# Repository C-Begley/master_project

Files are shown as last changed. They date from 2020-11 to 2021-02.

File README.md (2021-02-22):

# MEng Individual Project ENG5041PA Hardware and Software Emulation Testbed for CubeSat Design

## Abstract
CubeSats are praised for reducing the cost of access to space and increasing opportunities for universities and small organisations to carry out space related research. In principal, a small team with an innovative solution could rapidly develop and fly hardware in space using already existing building 'block' components. However, they still require technical electronic knowledge for the construction and testing of designs. While technical knowledge will always be required, especially on custom built CubeSats, this project aimed to reduce this barrier of entry, by providing a test bed framework to program and experiment with potential CubeSat designs.

The project has two main aims: the construction of physical devices for use in testing and developing accompanying software to help use these devices. The main physical device is a FlatSat, which aims to be generic and suitable for a range of projects. It uses PC/104 Plus connectors and has access to power and diagnostic connections. Alongside the FlatSat, there is a mainboard and battery board from an open source CubeSat design, which can be used to test other CubeSat subsystems. 

The project software helps schedule tasks to be run using the mainboard and FlatSat system. These tasks then act as emulations of an entire CubeSat subsystem. This allows for a subsystem to be tested, as if an entire CubeSat had already been constructed. The framework for programming and using this software, strives to be simple enough for those inexperienced with programming to be able to be use, while still giving enough complexity that most aspects of a CubeSat can be emulated.

To demonstrate the usability of the system, two demonstration boards have been constructed. These boards provide example emulations of payload and communication boards. They also provide a template that can be modified to construct and emulate other subsystems.  A demonstration task schedule has also been created to show how devices can interact with the software and mainboard from this project.

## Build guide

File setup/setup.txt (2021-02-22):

SETUP PYCUBED BOARD:
1.Follow the instructions on : https://www.notion.so/Programming-the-Bootloader-a5c2f6b50c3d459eaa0a4f00d8218365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
(In case site is taken down, see Programming the BootLoader.pdf)

2.The device should connect to a computer as a external drive. Transfer via USB all the files in software/Mainboard
(If it hasn't connected, try debugging with Atmel or following PyCubed FAQ/advice. I never got to run the Pycubed board(used Grand Central Metro M4 instead), so can't offer more advice)

SETUP MAIN PROGRAM:
OPTION ONE: Automatic Running
1. Rename the file `run_main.py` to main
2. Restart the device
3. The main program should run all tasks in the demo file

OPTION TWO: Manually running the code 
(This is often the best option, as main.py files can sometimes cause issue in Ciruit Python)

1.Run the code from a REPL programm
 `import run_main as m`

a. Linux users can use Picocom 
b. Mac users can use screen or Mu
c. Windows users can use Mu  
(Other programs may also work, this is not an exhaustive list)

Notes:
If you wish to use a different folder for running your code, 
replace the name PROJECT_FOLDER in the file run_main.py with something else.
 The new folder should follow the same structure and subfolders as demo

See Thesis Pgs.40-49 for more information on the options within a task, interupt and device file

SETUP DEMONSTRATION BOARDS:
The code for the demonstration boards is in MicroPython, to support using the device as a slave.
Some Circuit Python libraries etc will not work on these boards and vice versa

The boards provided in the lab should already be flashed. If not follow the steps in Flashing.txt (they are written for a Linux device)

To transfer files to these boards, ampy has to be used 
e.g `ampy -- port /deb/ttyUSB0 coms_IWC.py`
(This should work on Mac or Linux but may need to be installed)

There are two programs that can be run on the boards
`payload_main.py` and `coms_main.py` 

To use the payload add the `payload_main.py`, `demo_adc.py` and `payload_I2C.py`

To use the communication board add `coms_main.py` and `coms_I2C.py`

To run on a terminal, use a REPL program (see above)
`import payload_main as pld`
           or
`import coms_main as cms`

You can also just run the commands inside a REPL terminal

Like with the other files, you can rename them to main. However, this omes with the caveat the boards may need reflashing

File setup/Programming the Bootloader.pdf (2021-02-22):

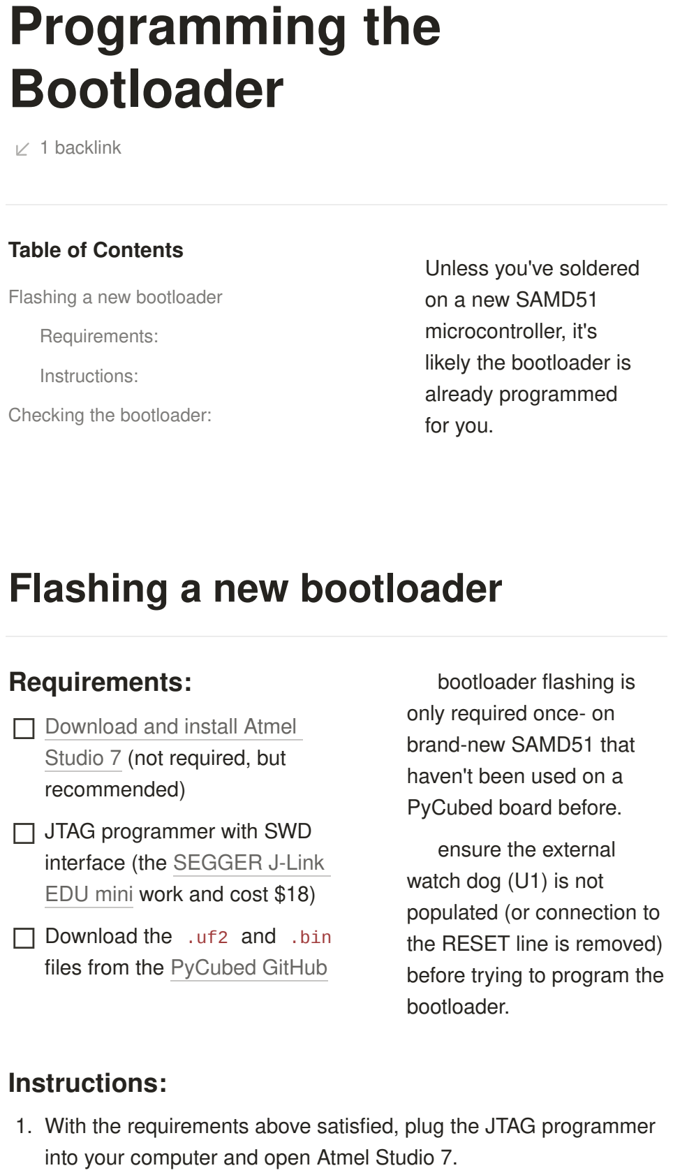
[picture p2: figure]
1 backlink; Programming the Bootloader; Table of Contents; Flashing a new bootloader; Requirements:; Instructions:; Checking the bootloader:; Unless you've soldered on a new SAMD51; microcontroller, it's; likely the bootloader is; already programmed for you.; (not required, but; recommended); JTAG programmer with SWD; interface (the work and cost $18); Download the .uf2 and .bin files from the; bootloader flashing is; only required once- on brand-new SAMD51 that; haven't been used on a PyCubed board before.; ensure the external; watch dog (U1) is not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

1. With the requirements above satisfied, plug the JTAG programmer into your computer and open Atmel Studio 7.
Programming the Bootloader | https://www.notion.so/Programming-the-Bootloader-a5...
1 of 6 | 22/02/2021, 15:24

2. Navigate to Tools → Device Programming, as shown:
3. Select the appropriate Tool and Device from the drop-down menus and click apply.

make sure to choose the correct microcontroller part number. Visually check the part markings on the SAMD51 to confirm if it's the SAMD51x19 or SAMD51x20.

4. Navigate to "Memories" on the left-hand side.
5. Uncheck the "Erase Flash before programming" box, and then click the "..." button, as shown:
6. Navigate to the directory you saved the GitHub firmware files, and change the file parameters from "Programming Files" to "Binary" and shown:

7. Select the .bin file downloaded previously and click the "Open" button:

8. Now make the following connections to the PyCubed board. If you're careful, you can avoid soldering header-pins to the board by just holding jumper-wire pins (or pogo pins, if you have them) against the through-holes during programming. When in doubt, solder the header pins.

Required Connections:

Main micro USB cable (to provide power)

Note: it's good practice to use a multimeter and confirm 3.3V is present when the USB connection is made to the PyCubed board. If the voltage doesn't read 3.3V between "3V3" and "GND" you need to troubleshoot that first.

VTref (connected to 3V3)

TMS (connected to SWDIO)

TCK (connected to SWCLK)

GND (connected to GND)

9. With the connections made, return to Atmel Studio 7 and click the "Read" button. A device signature should populate. If an error appears, check connections and troubleshoot the specific error message.

Common Errors

10. After receiving a device signature, click the "Program" button. Programming should only take a few moments.
11. Successful bootloader programming will trigger the PyCubed board to reboot. After a few moments, the board should mount to the computer as a PYCUBEDBOOT drive.

### Flashing the Firmware:

12. Drag the CircuitPython firmware .uf2 file downloaded previously to the PYCUBEDBOOT drive:
13. As soon as the file is done transferring, the board will reboot again and mount as CIRCUITPY or PYCUBED and is now a functioning CircuitPython board. Congratulations!
Note: now is a good time to load the | to the lib
folder as described in: Adding/Updating Libraries
14. The firmware loaded in step 12 makes it possible to safely solder the external watch dog (U1) onto the board.

# Checking the bootloader:

1. Connect the PyCubed board to your computer via USB
2. Quickly double-click the "RESET" button located on the top of the board

The pace of the double-click can be difficult. If it doesn't work,

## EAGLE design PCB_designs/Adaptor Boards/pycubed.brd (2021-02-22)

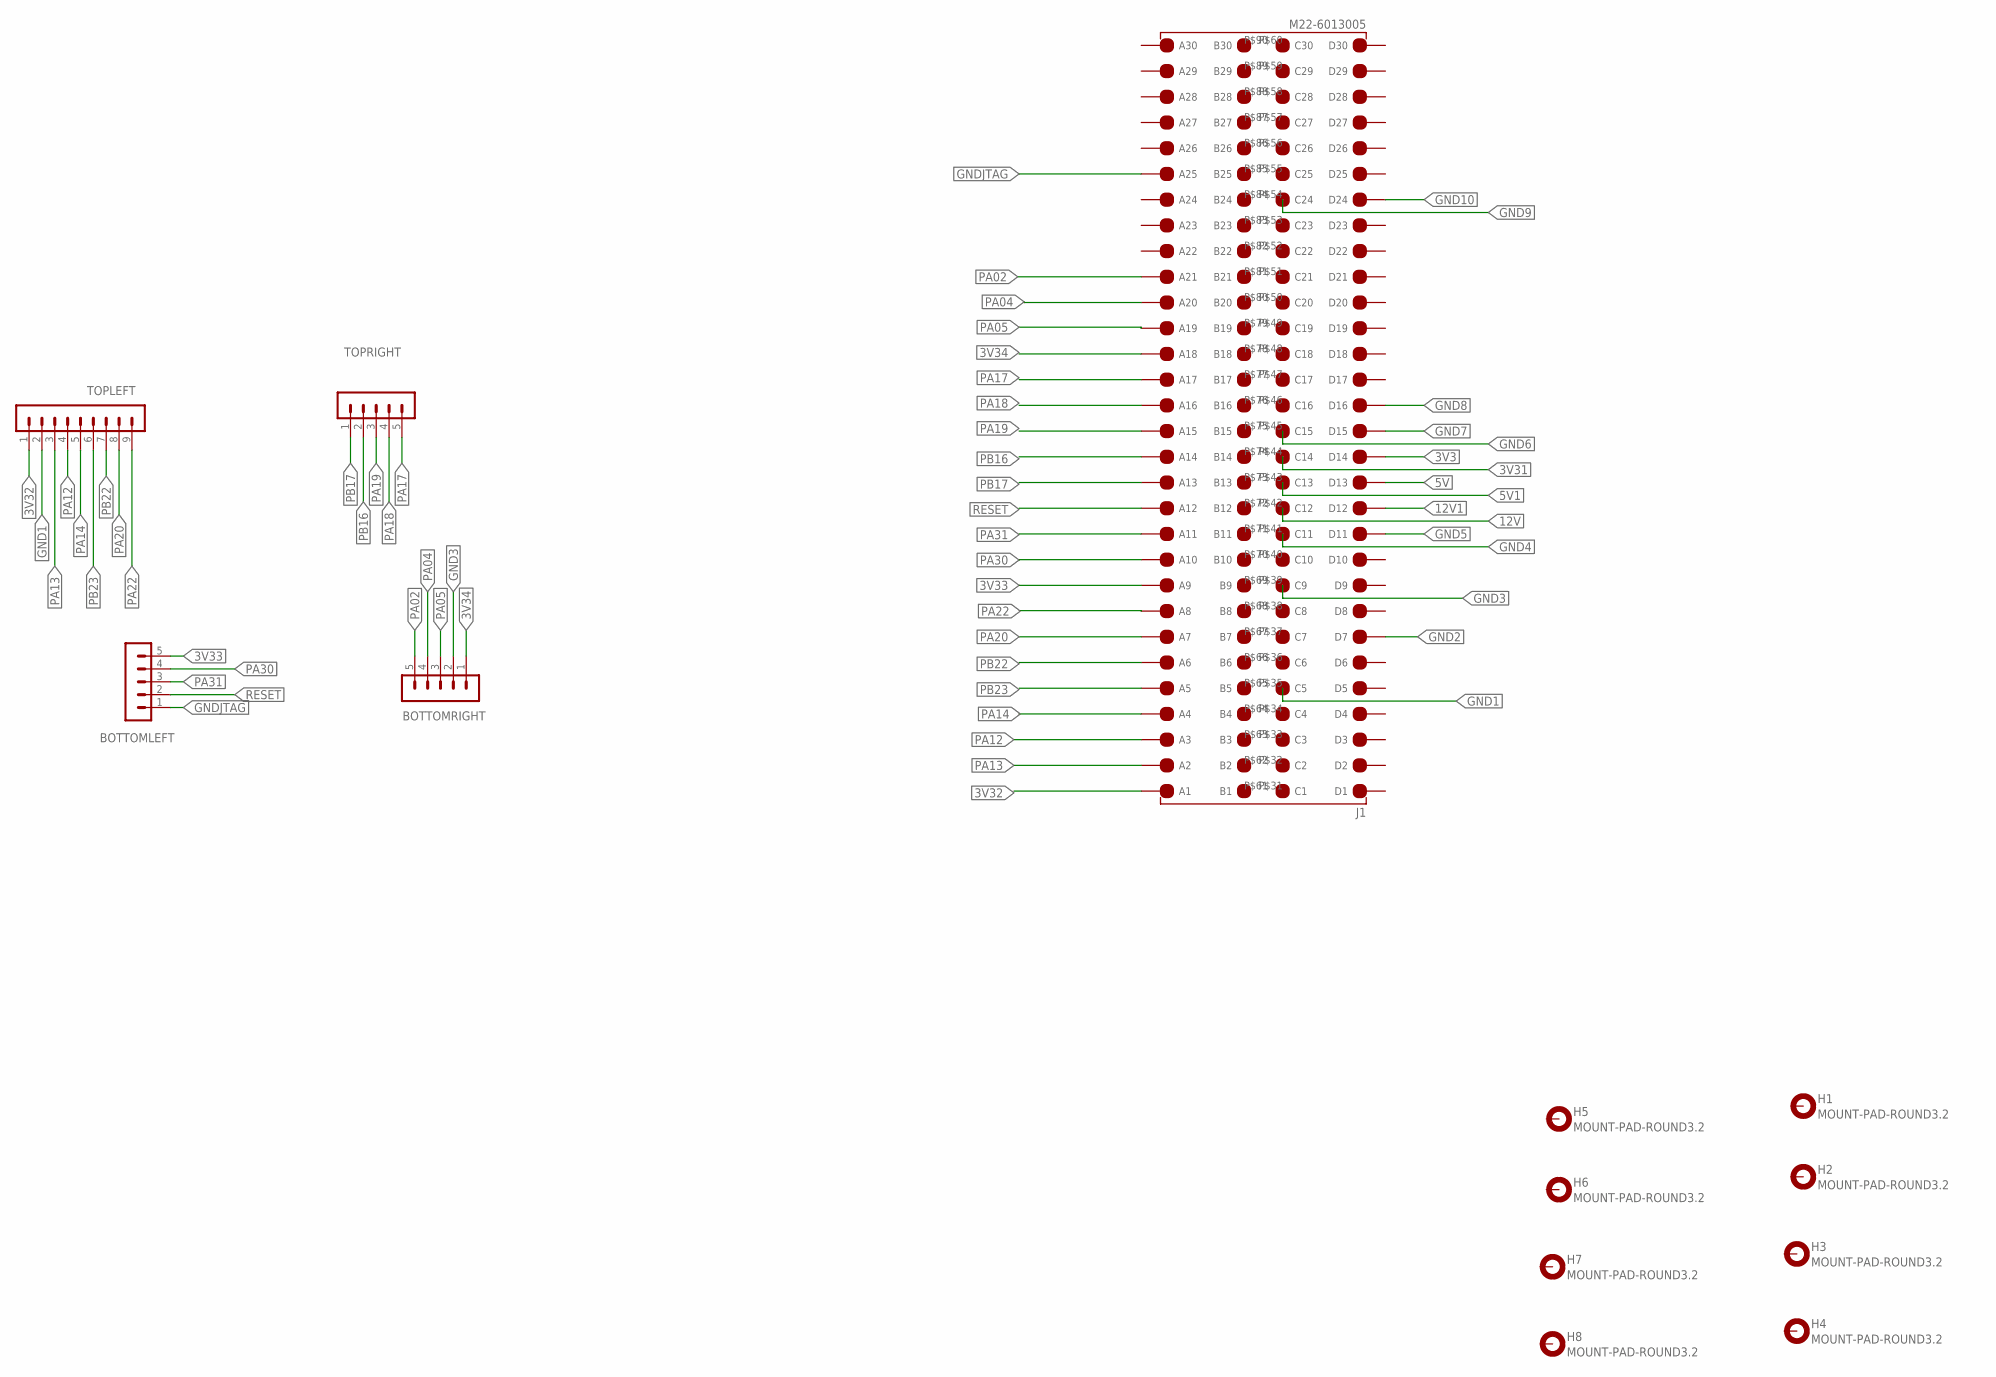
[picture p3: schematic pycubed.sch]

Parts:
BOTTOMLEFT: MA05-1
BOTTOMRIGHT: MA05-1
H1, H2, H3, H4, H5, H6, H7, H8: MOUNT-PAD-ROUND3.2; 3,2-PAD
J1: M22-6013005; RHDR120W55P200_4X30_6020X820X9
TOPLEFT: MA09-1
TOPRIGHT: MA05-1

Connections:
3V3: J1.P$14 (D14)
3V31: J1.P$44 (C14)
3V32: J1.P$91 (A1), TOPLEFT.1
3V33: BOTTOMLEFT.5, J1.P$99 (A9)
3V34: BOTTOMRIGHT.1, J1.P$108 (A18)
5V: J1.P$13 (D13)
5V1: J1.P$43 (C13)
12V: J1.P$42 (C12)
12V1: J1.P$12 (D12)
GND1: J1.P$35 (C5), TOPLEFT.2
GND2: J1.P$7 (D7)
GND3: BOTTOMRIGHT.2, J1.P$39 (C9)
GND4: J1.P$41 (C11)
GND5: J1.P$11 (D11)
GND6: J1.P$45 (C15)
GND7: J1.P$15 (D15)
GND8: J1.P$16 (D16)
GND9: J1.P$54 (C24)
GND10: J1.P$24 (D24)
GNDJTAG: BOTTOMLEFT.1, J1.P$115 (A25)
PA02: BOTTOMRIGHT.5, J1.P$111 (A21)
PA04: BOTTOMRIGHT.4, J1.P$110 (A20)
PA05: BOTTOMRIGHT.3, J1.P$109 (A19)
PA12: J1.P$93 (A3), TOPLEFT.4
PA13: J1.P$92 (A2), TOPLEFT.3
PA14: J1.P$94 (A4), TOPLEFT.5
PA17: J1.P$107 (A17), TOPRIGHT.5
PA18: J1.P$106 (A16), TOPRIGHT.4
PA19: J1.P$105 (A15), TOPRIGHT.3
PA20: J1.P$97 (A7), TOPLEFT.8
PA22: J1.P$98 (A8), TOPLEFT.9
PA30: BOTTOMLEFT.4, J1.P$100 (A10)
PA31: BOTTOMLEFT.3, J1.P$101 (A11)
PB16: J1.P$104 (A14), TOPRIGHT.2
PB17: J1.P$103 (A13), TOPRIGHT.1
PB22: J1.P$96 (A6), TOPLEFT.7
PB23: J1.P$95 (A5), TOPLEFT.6
RESET: BOTTOMLEFT.2, J1.P$102 (A12)

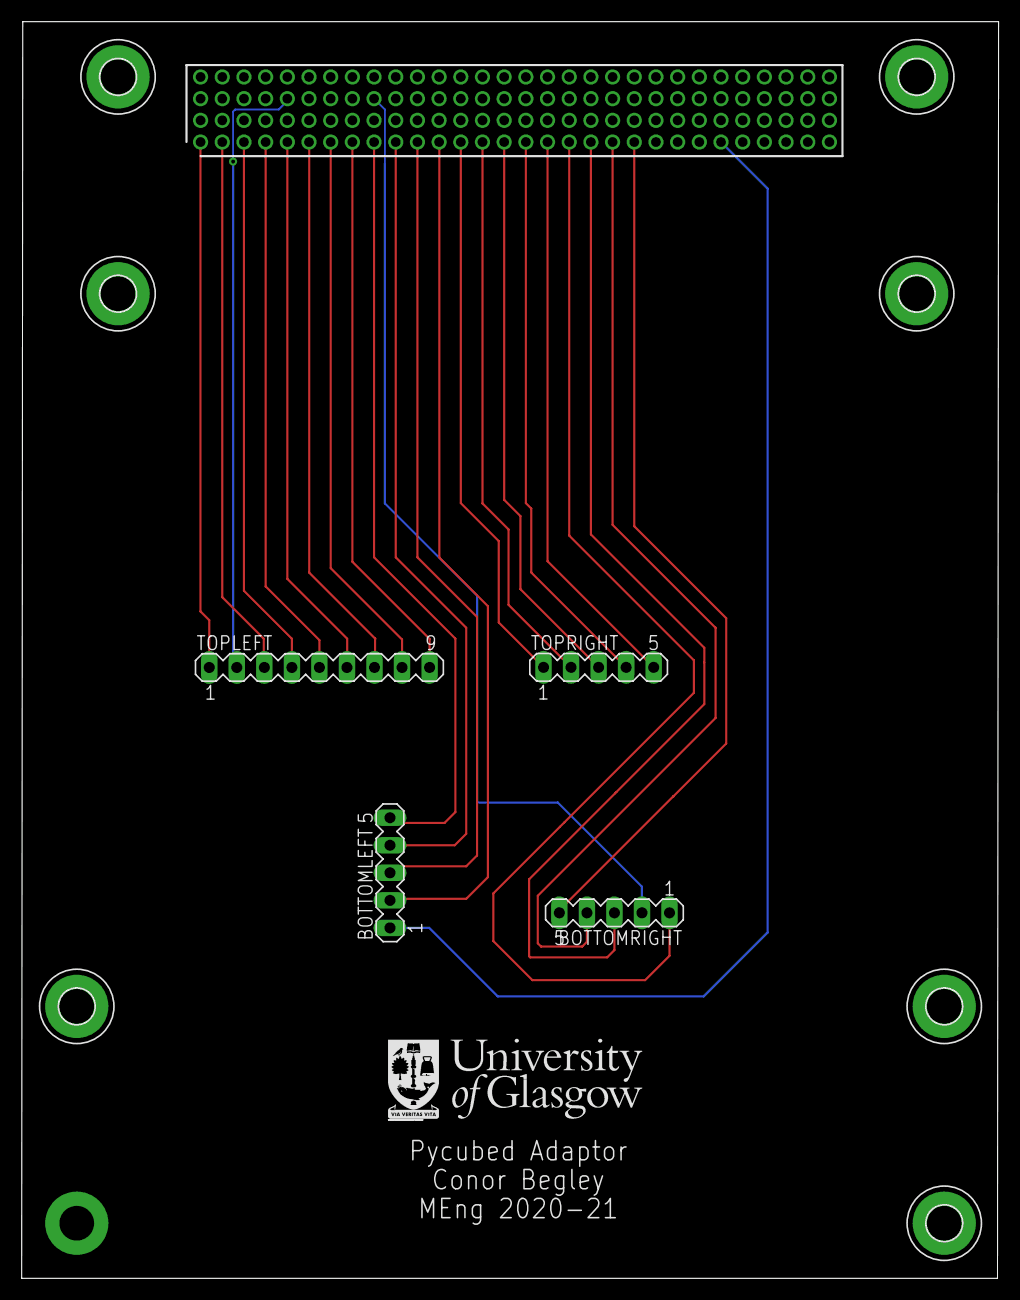
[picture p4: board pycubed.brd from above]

Board: 2 copper layers, 90.1 x 115.9 mm, 13 parts (1 on the bottom side), 24 nets.

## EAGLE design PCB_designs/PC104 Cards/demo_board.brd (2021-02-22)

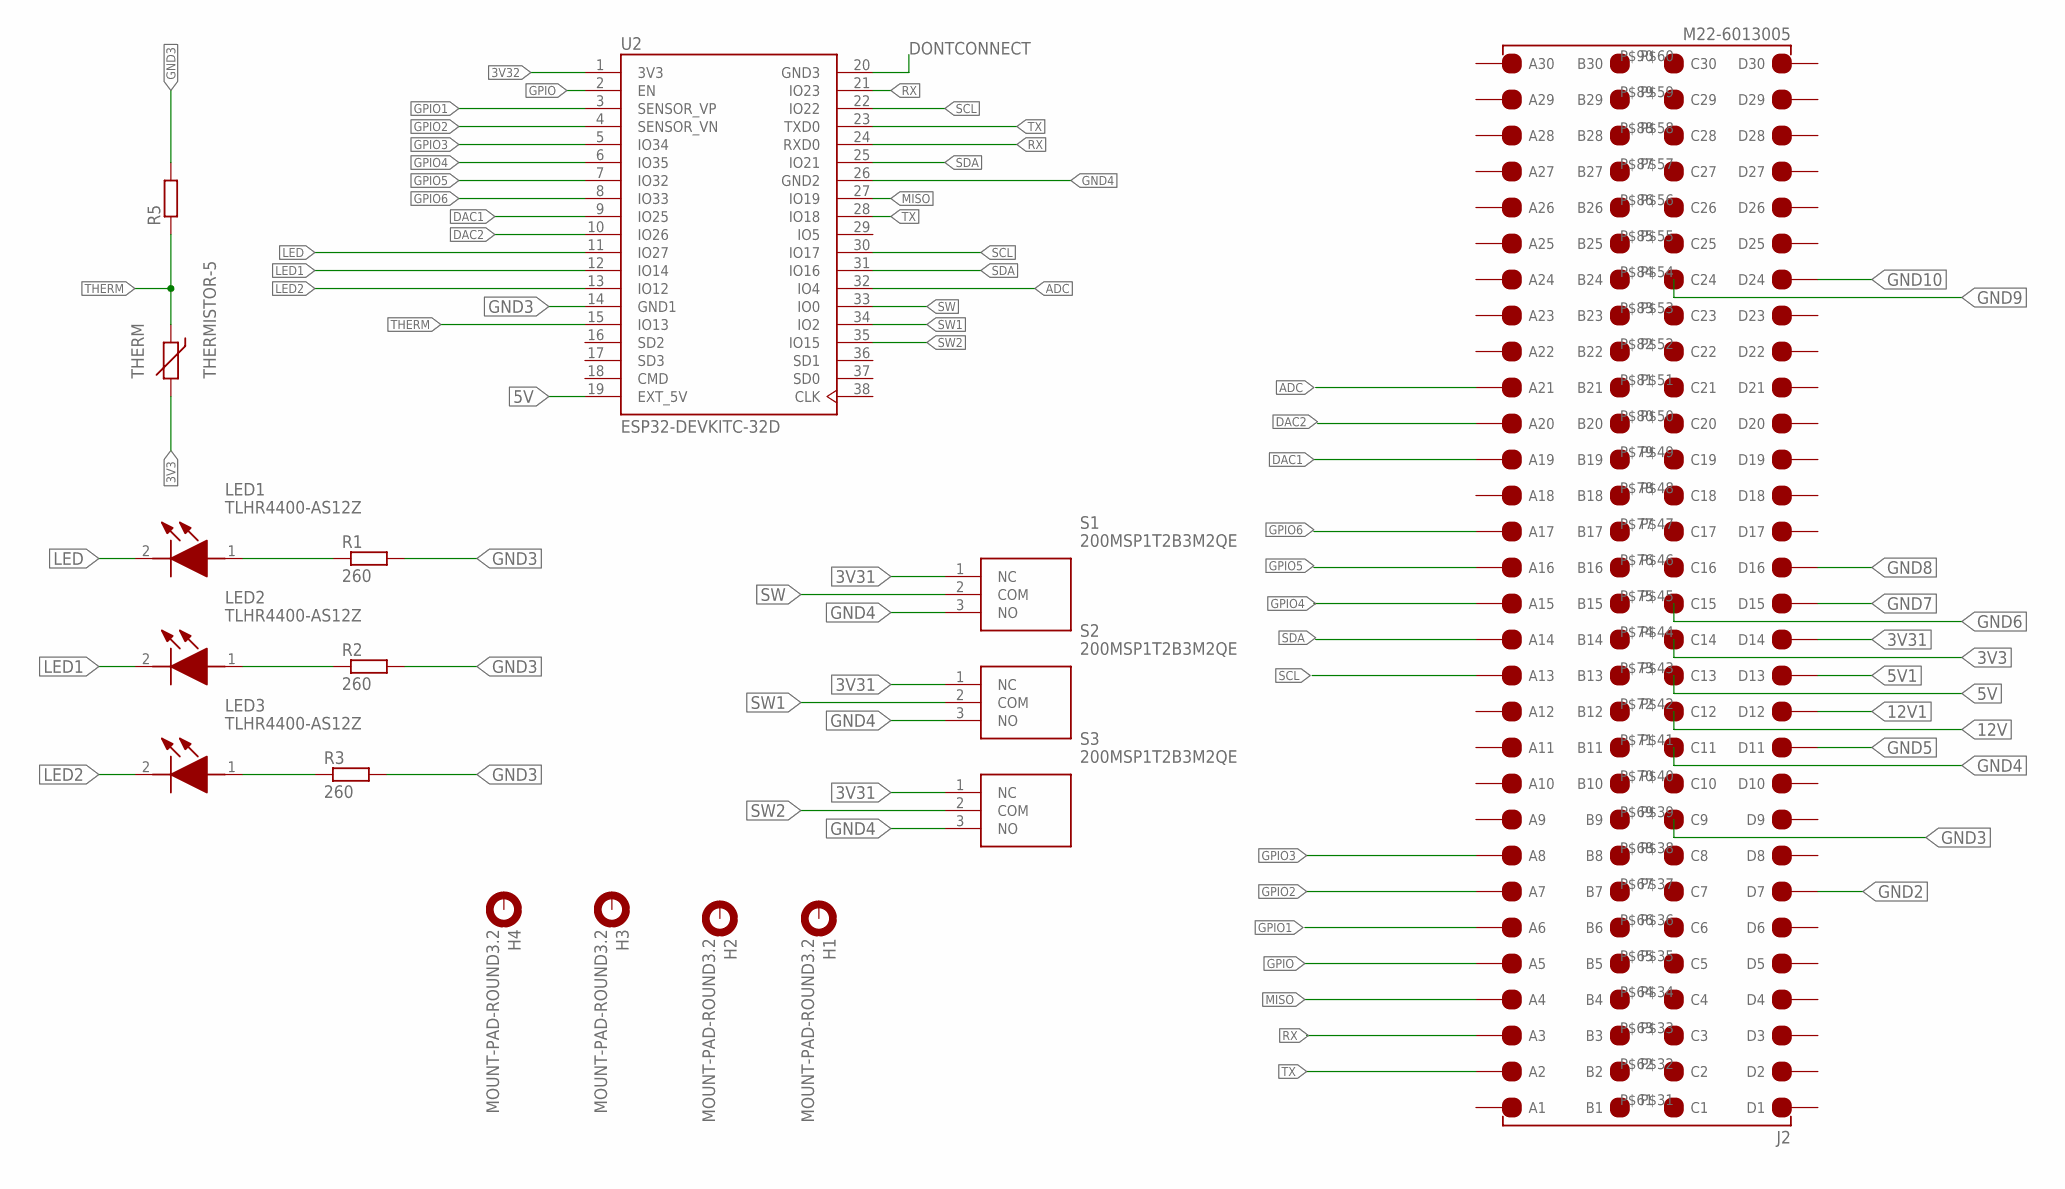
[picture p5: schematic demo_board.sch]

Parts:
H1, H2, H3, H4: MOUNT-PAD-ROUND3.2; 3,2-PAD
J2: M22-6013005; RHDR120W55P200_4X30_6020X820X9
LED1, LED2, LED3: TLHR4400-AS12Z; TLHR4400AS12Z
R1, R2, R3: 260; 0204/7
R5: 130; 0204/7
S1, S2, S3: 200MSP1T2B3M2QE
THERM: THERMISTOR-5; R-5
U2: ESP32-DEVKITC-32D; MODULE_ESP32-DEVKITC-32D

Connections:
3V3: J2.P$44 (C14), THERM.2
3V31: J2.P$14 (D14), S1.1 (NC), S2.1 (NC), S3.1 (NC)
3V32: U2.1 (3V3)
5V: J2.P$43 (C13), U2.19 (EXT_5V)
5V1: J2.P$13 (D13)
12V: J2.P$42 (C12)
12V1: J2.P$12 (D12)
ADC: J2.P$111 (A21), U2.32 (IO4)
DAC1: J2.P$109 (A19), U2.9 (IO25)
DAC2: J2.P$110 (A20), U2.10 (IO26)
DONTCONNECT: U2.20 (GND3)
GND2: J2.P$7 (D7)
GND3: J2.P$39 (C9), R1.2, R2.2, R3.2, R5.2, U2.14 (GND1)
GND4: J2.P$41 (C11), S1.3 (NO), S2.3 (NO), S3.3 (NO), U2.26 (GND2)
GND5: J2.P$11 (D11)
GND6: J2.P$45 (C15)
GND7: J2.P$15 (D15)
GND8: J2.P$16 (D16)
GND9: J2.P$54 (C24)
GND10: J2.P$24 (D24)
GPIO: J2.P$95 (A5), U2.2 (EN)
GPIO1: J2.P$96 (A6), U2.3 (SENSOR_VP)
GPIO2: J2.P$97 (A7), U2.4 (SENSOR_VN)
GPIO3: J2.P$98 (A8), U2.5 (IO34)
GPIO4: J2.P$105 (A15), U2.6 (IO35)
GPIO5: J2.P$106 (A16), U2.7 (IO32)
GPIO6: J2.P$107 (A17), U2.8 (IO33)
LED: LED1.2 (K), U2.11 (IO27)
LED1: LED2.2 (K), U2.12 (IO14)
LED2: LED3.2 (K), U2.13 (IO12)
MISO: J2.P$94 (A4), U2.27 (IO19)
unnamed: LED1.1 (A), R1.1
unnamed: LED2.1 (A), R2.1
unnamed: LED3.1 (A), R3.1
RX: J2.P$93 (A3), U2.21 (IO23), U2.24 (RXD0)
SCL: J2.P$103 (A13), U2.22 (IO22), U2.30 (IO17)
SDA: J2.P$104 (A14), U2.25 (IO21), U2.31 (IO16)
SW: S1.2 (COM), U2.33 (IO0)
SW1: S2.2 (COM), U2.34 (IO2)
SW2: S3.2 (COM), U2.35 (IO15)
THERM: R5.1, THERM.1, U2.15 (IO13)
TX: J2.P$92 (A2), U2.23 (TXD0), U2.28 (IO18)

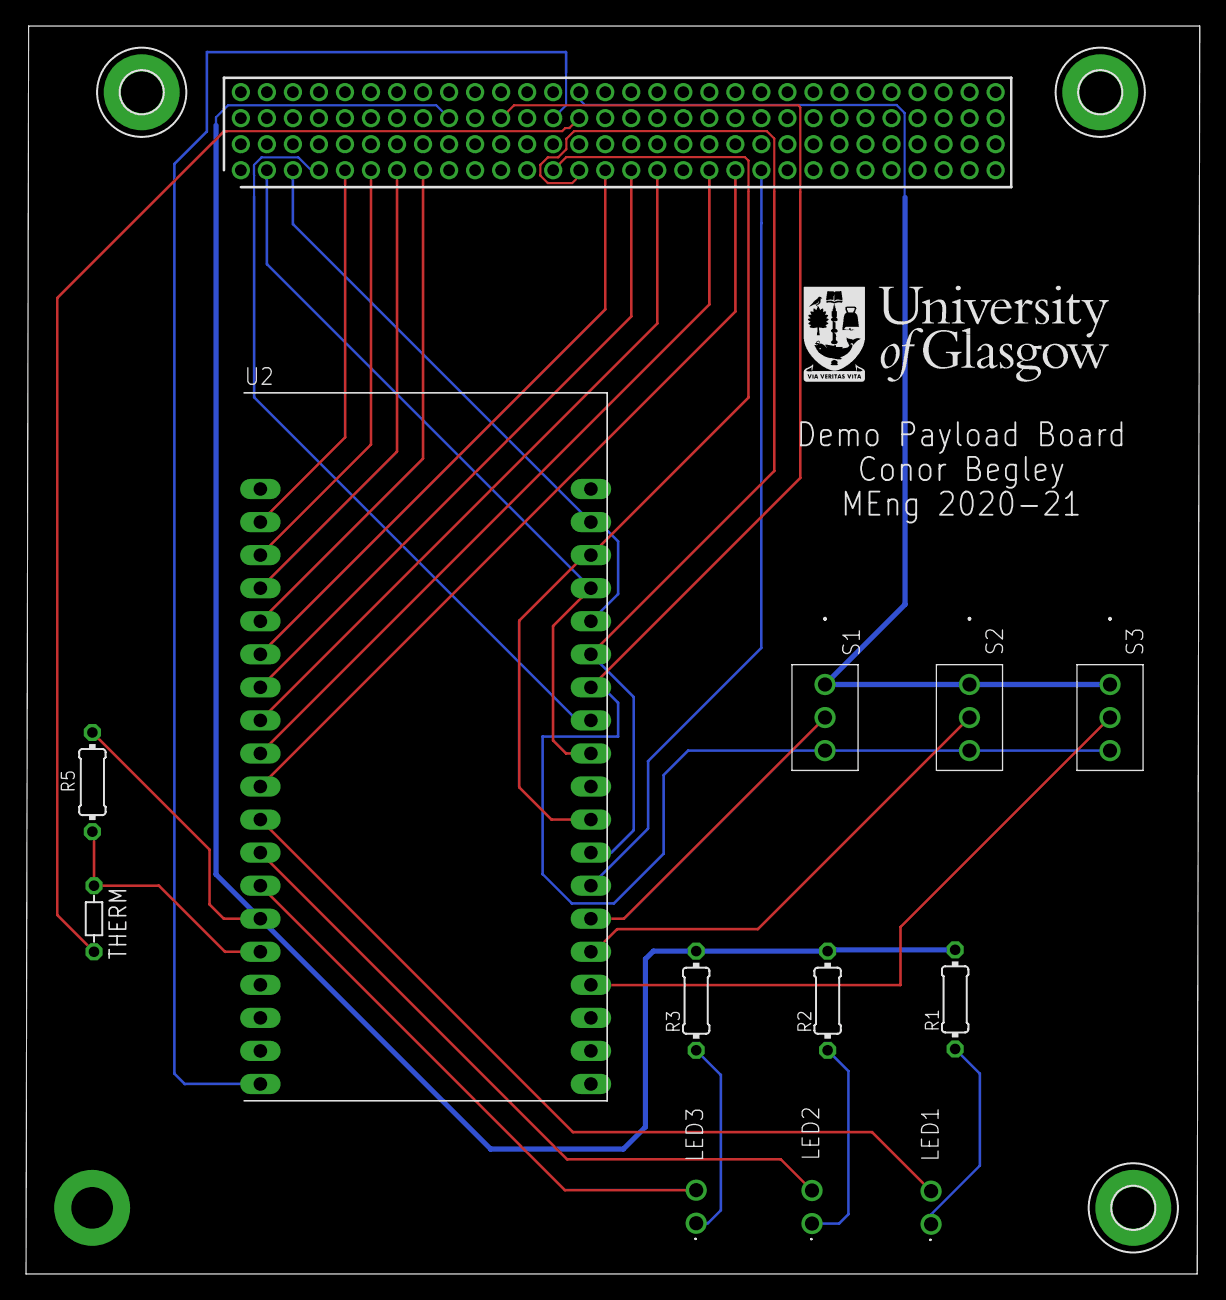
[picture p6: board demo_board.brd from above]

Board: 2 copper layers, 90.2 x 95.9 mm, 17 parts (1 on the bottom side), 30 nets.

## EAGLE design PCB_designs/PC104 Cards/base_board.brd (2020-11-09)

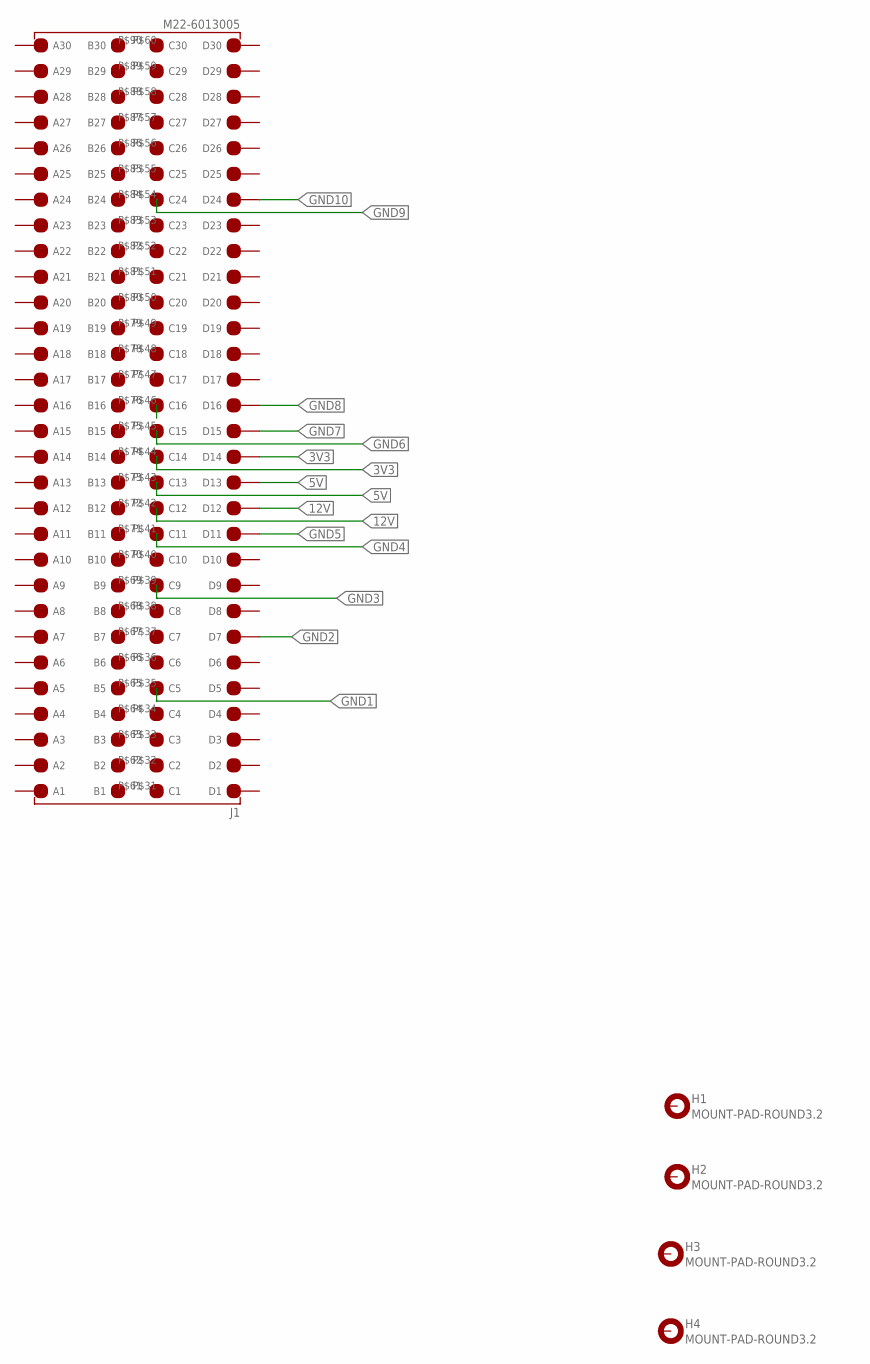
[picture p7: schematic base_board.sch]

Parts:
H1, H2, H3, H4: MOUNT-PAD-ROUND3.2; 3,2-PAD
J1: M22-6013005; RHDR120W55P200_4X30_6020X820X9

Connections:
3V3: J1.P$14 (D14), J1.P$44 (C14)
5V: J1.P$13 (D13), J1.P$43 (C13)
12V: J1.P$12 (D12), J1.P$42 (C12)
GND1: J1.P$35 (C5)
GND2: J1.P$7 (D7)
GND3: J1.P$39 (C9)
GND4: J1.P$41 (C11)
GND5: J1.P$11 (D11)
GND6: J1.P$45 (C15)
GND7: J1.P$15 (D15)
GND8: J1.P$16 (D16), J1.P$46 (C16)
GND9: J1.P$54 (C24)
GND10: J1.P$24 (D24)

Board: 2 copper layers, 5 parts (1 on the bottom side), 4 nets, no tracks yet.

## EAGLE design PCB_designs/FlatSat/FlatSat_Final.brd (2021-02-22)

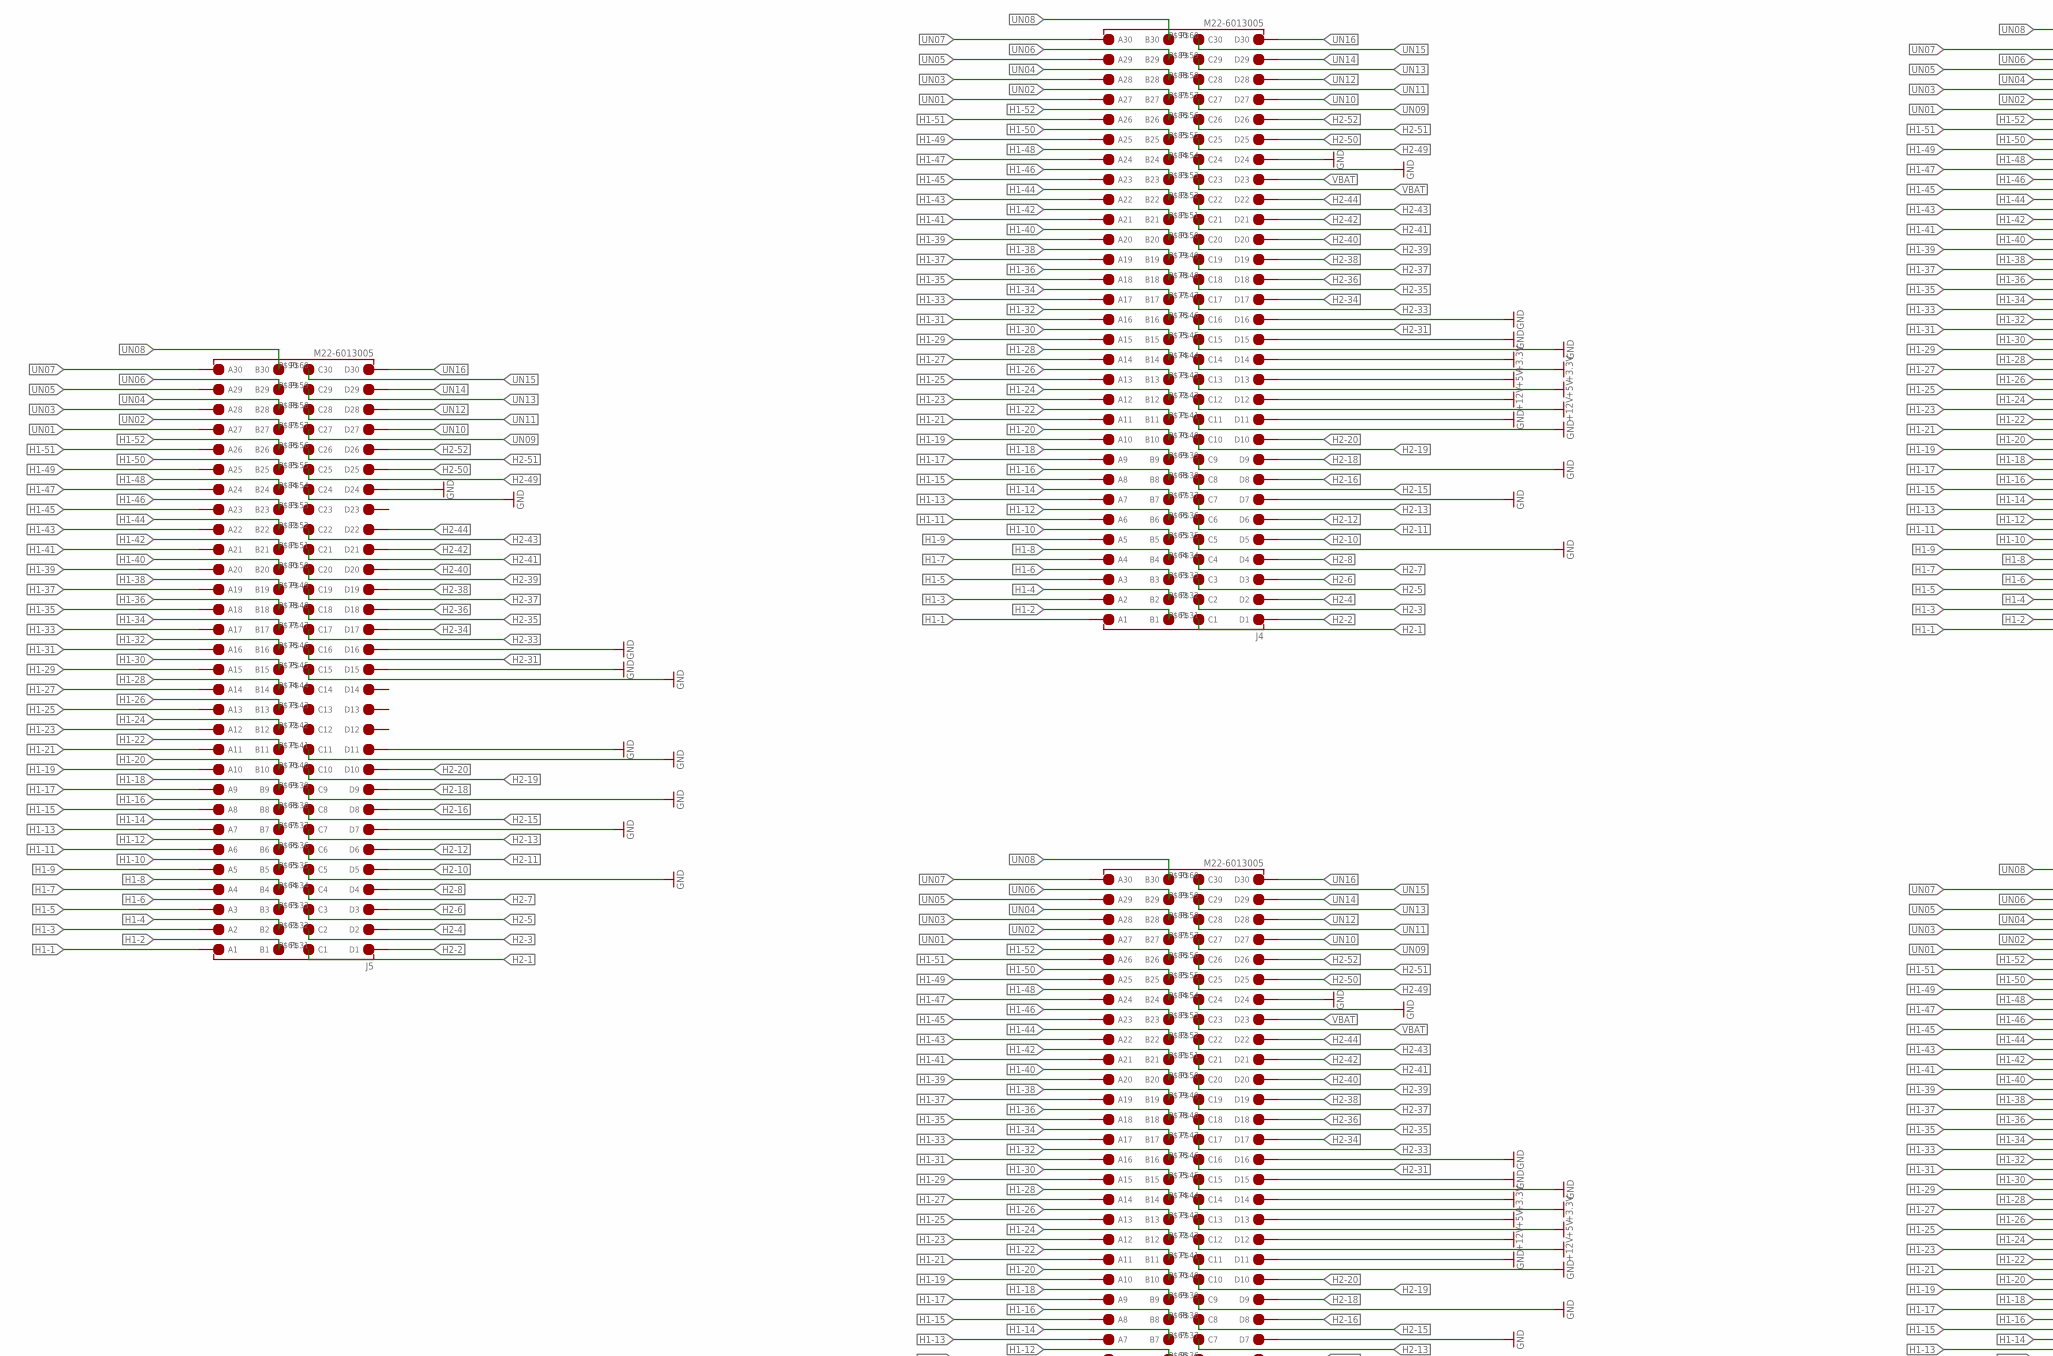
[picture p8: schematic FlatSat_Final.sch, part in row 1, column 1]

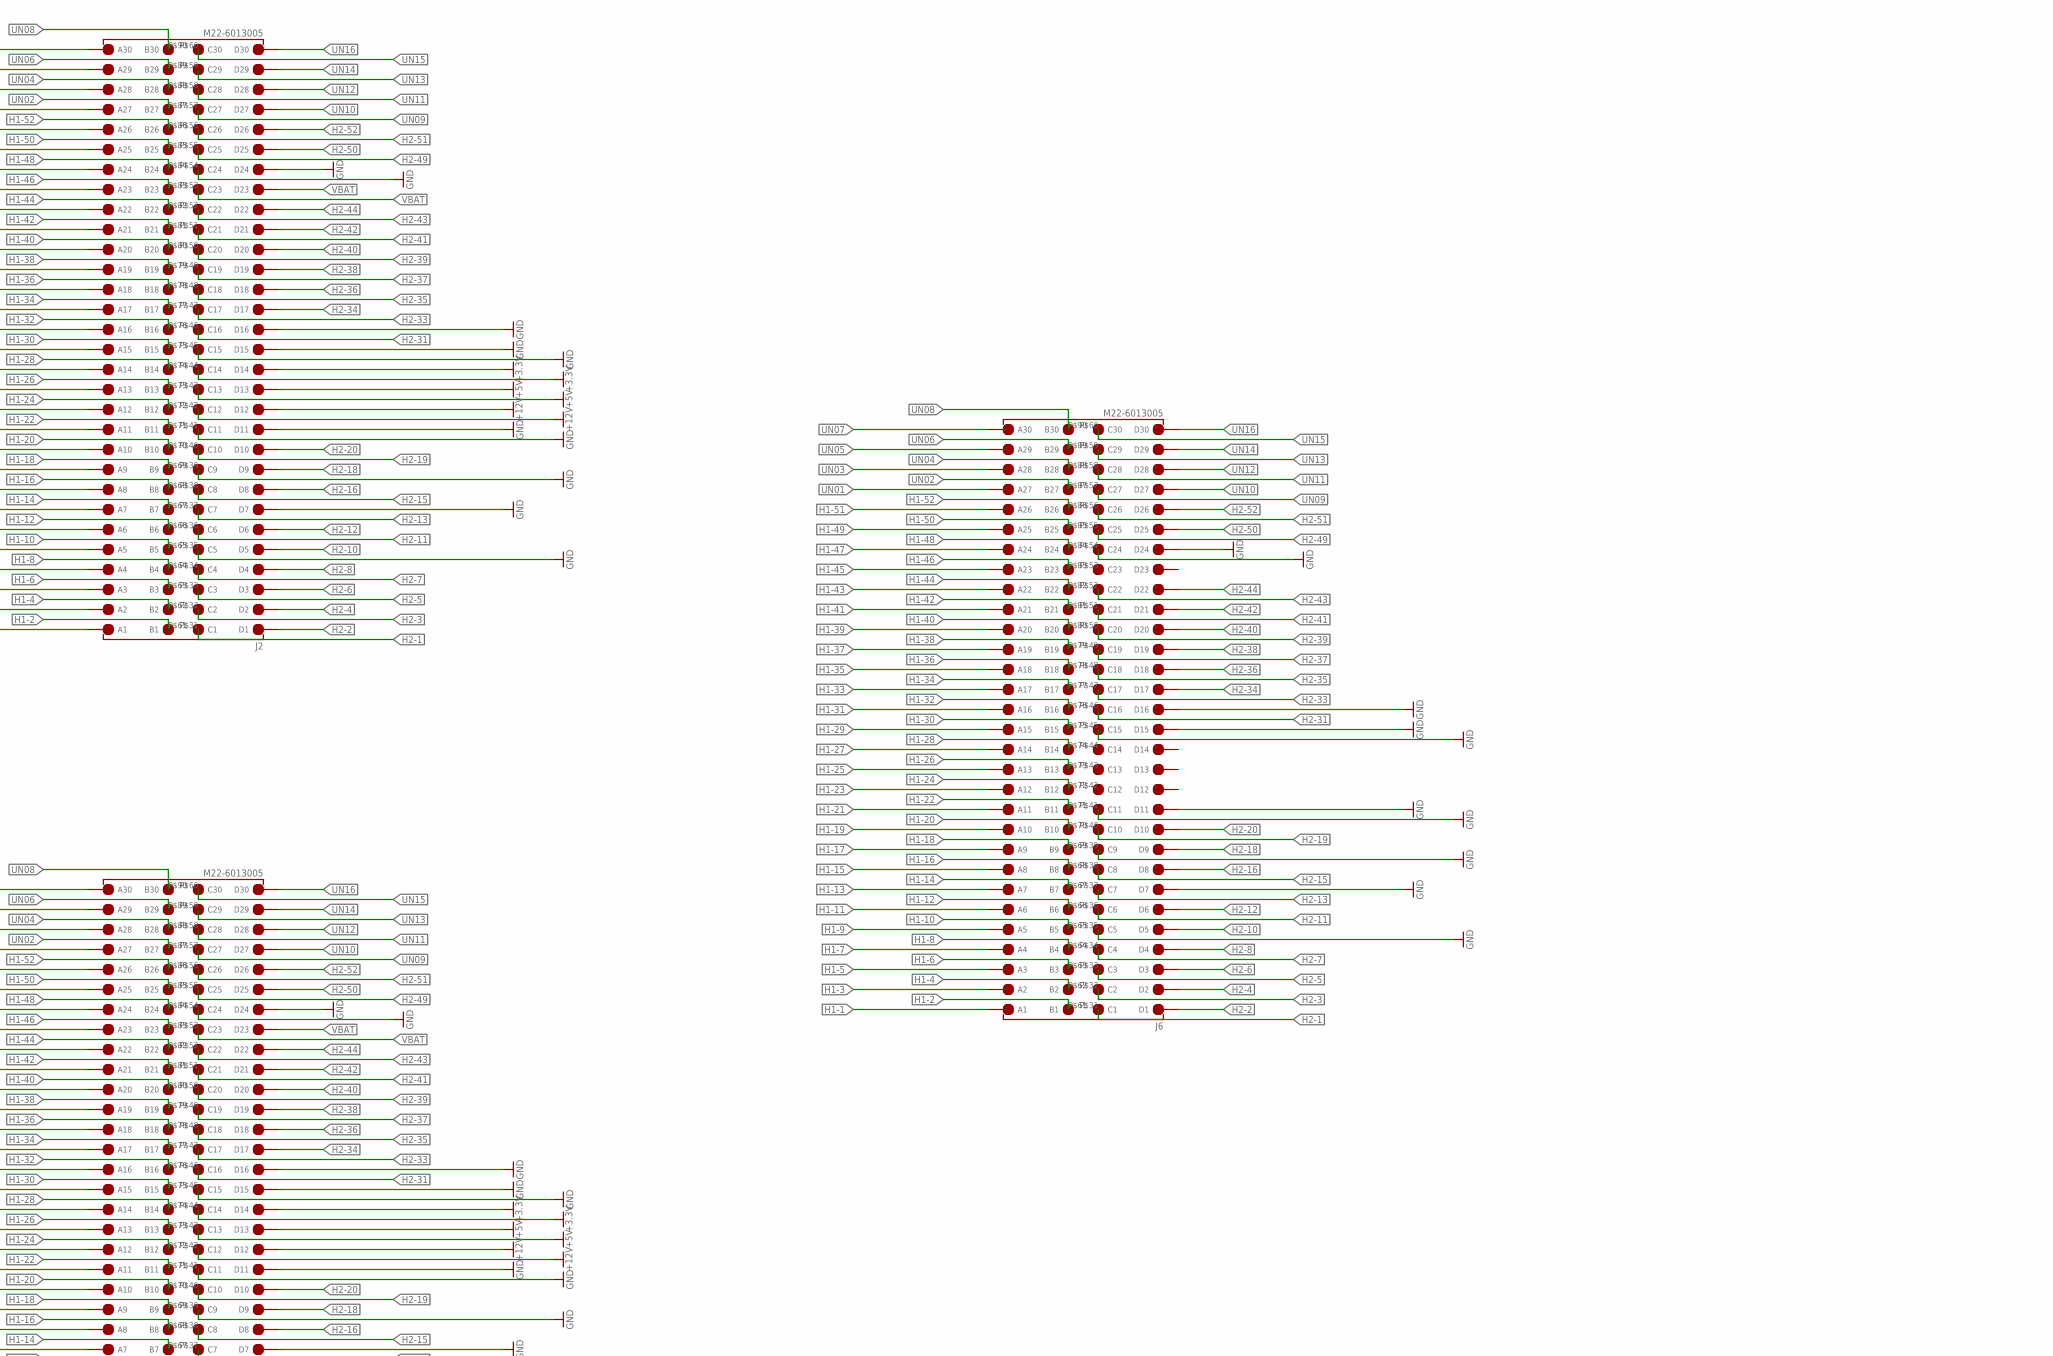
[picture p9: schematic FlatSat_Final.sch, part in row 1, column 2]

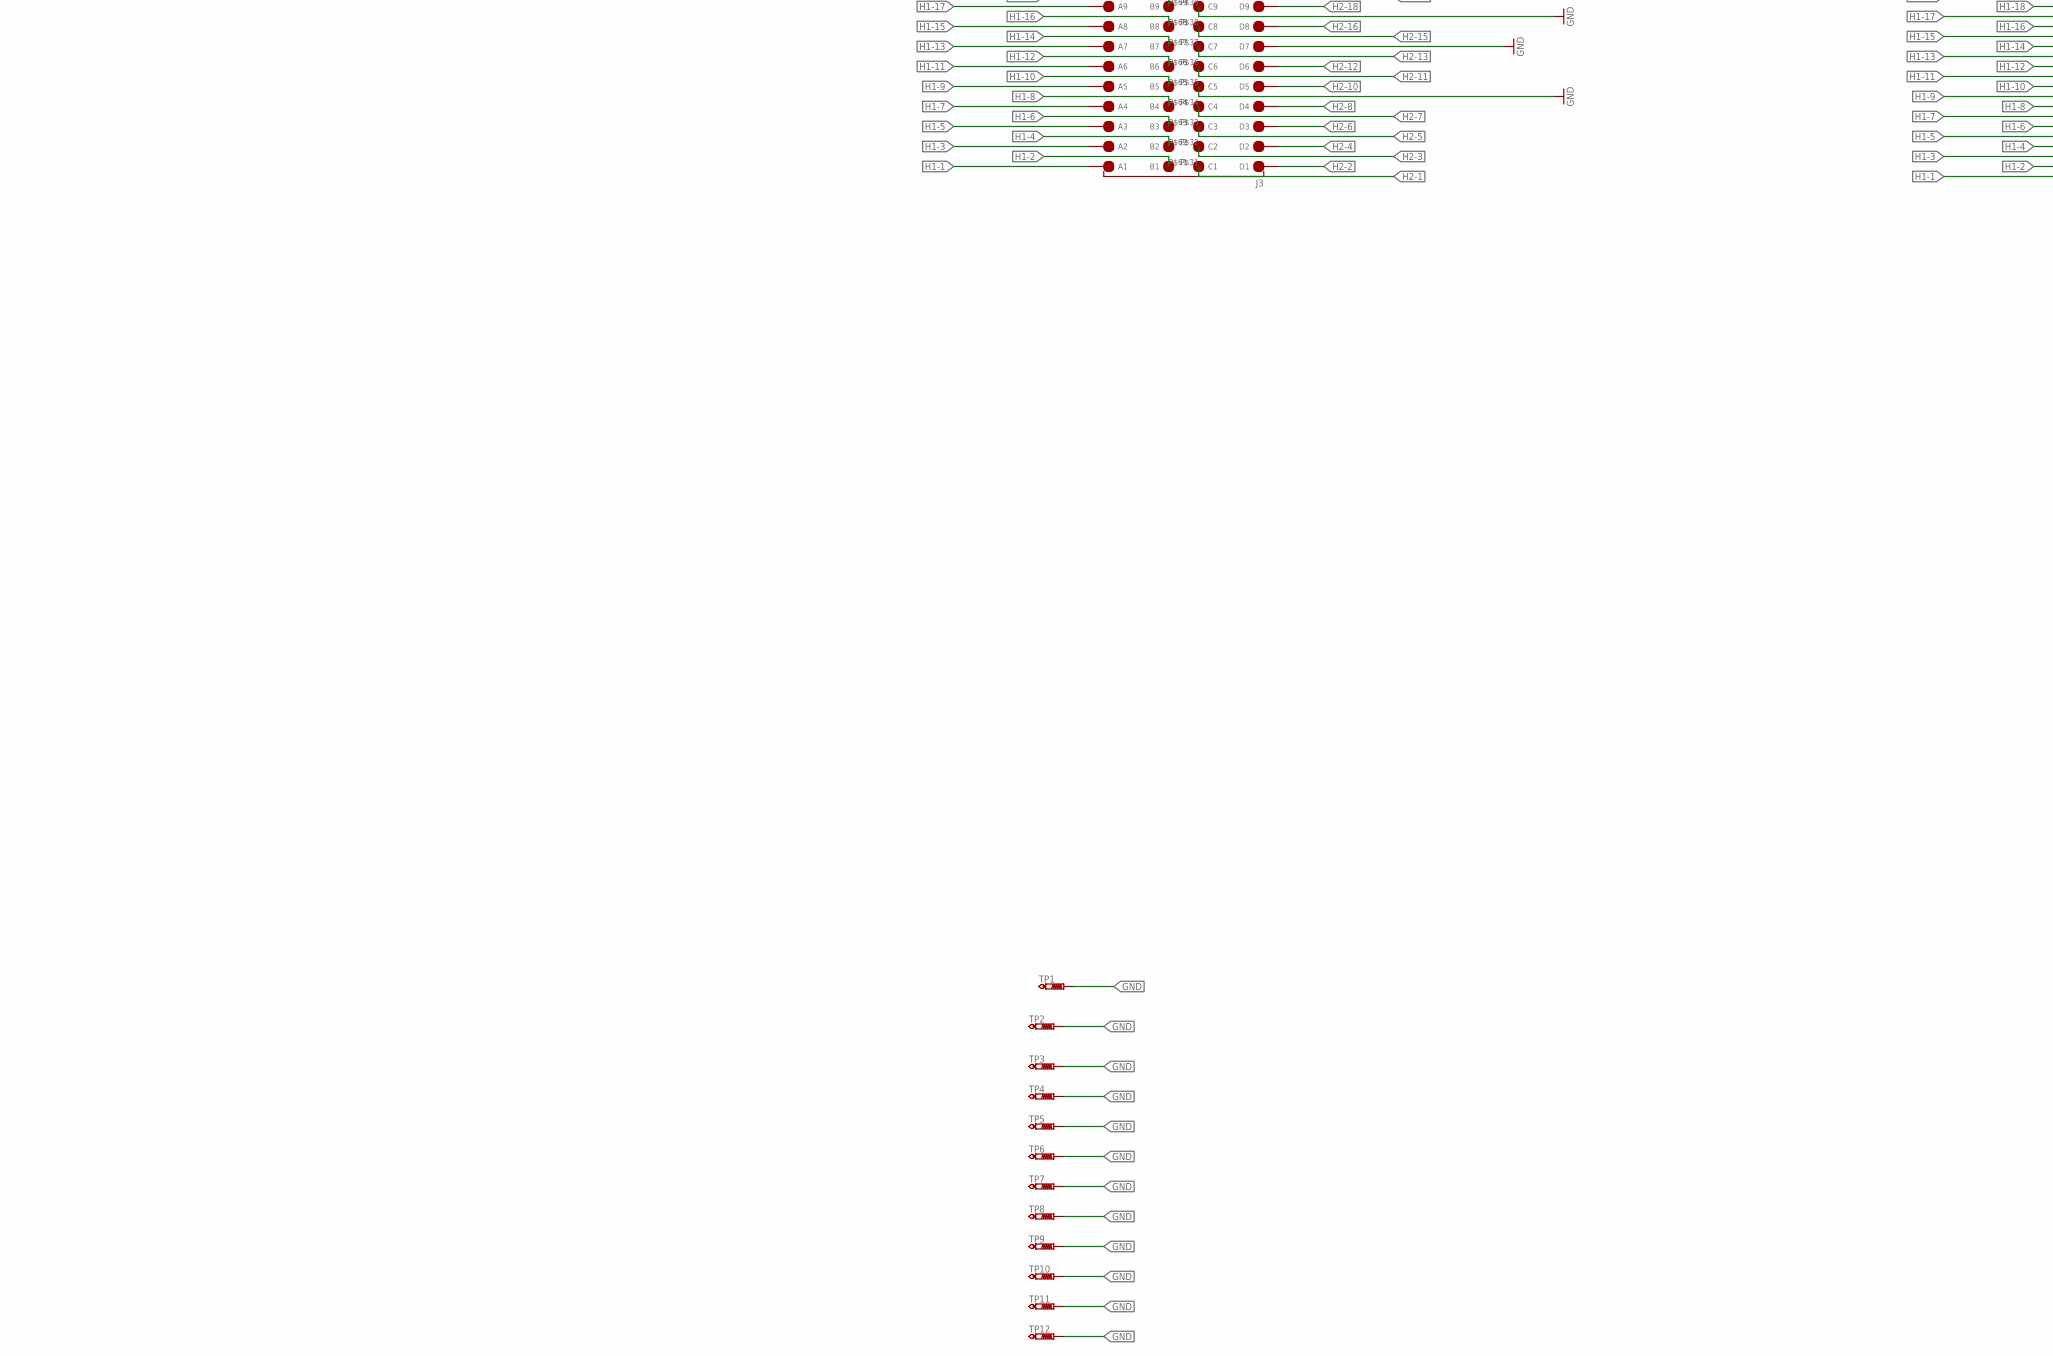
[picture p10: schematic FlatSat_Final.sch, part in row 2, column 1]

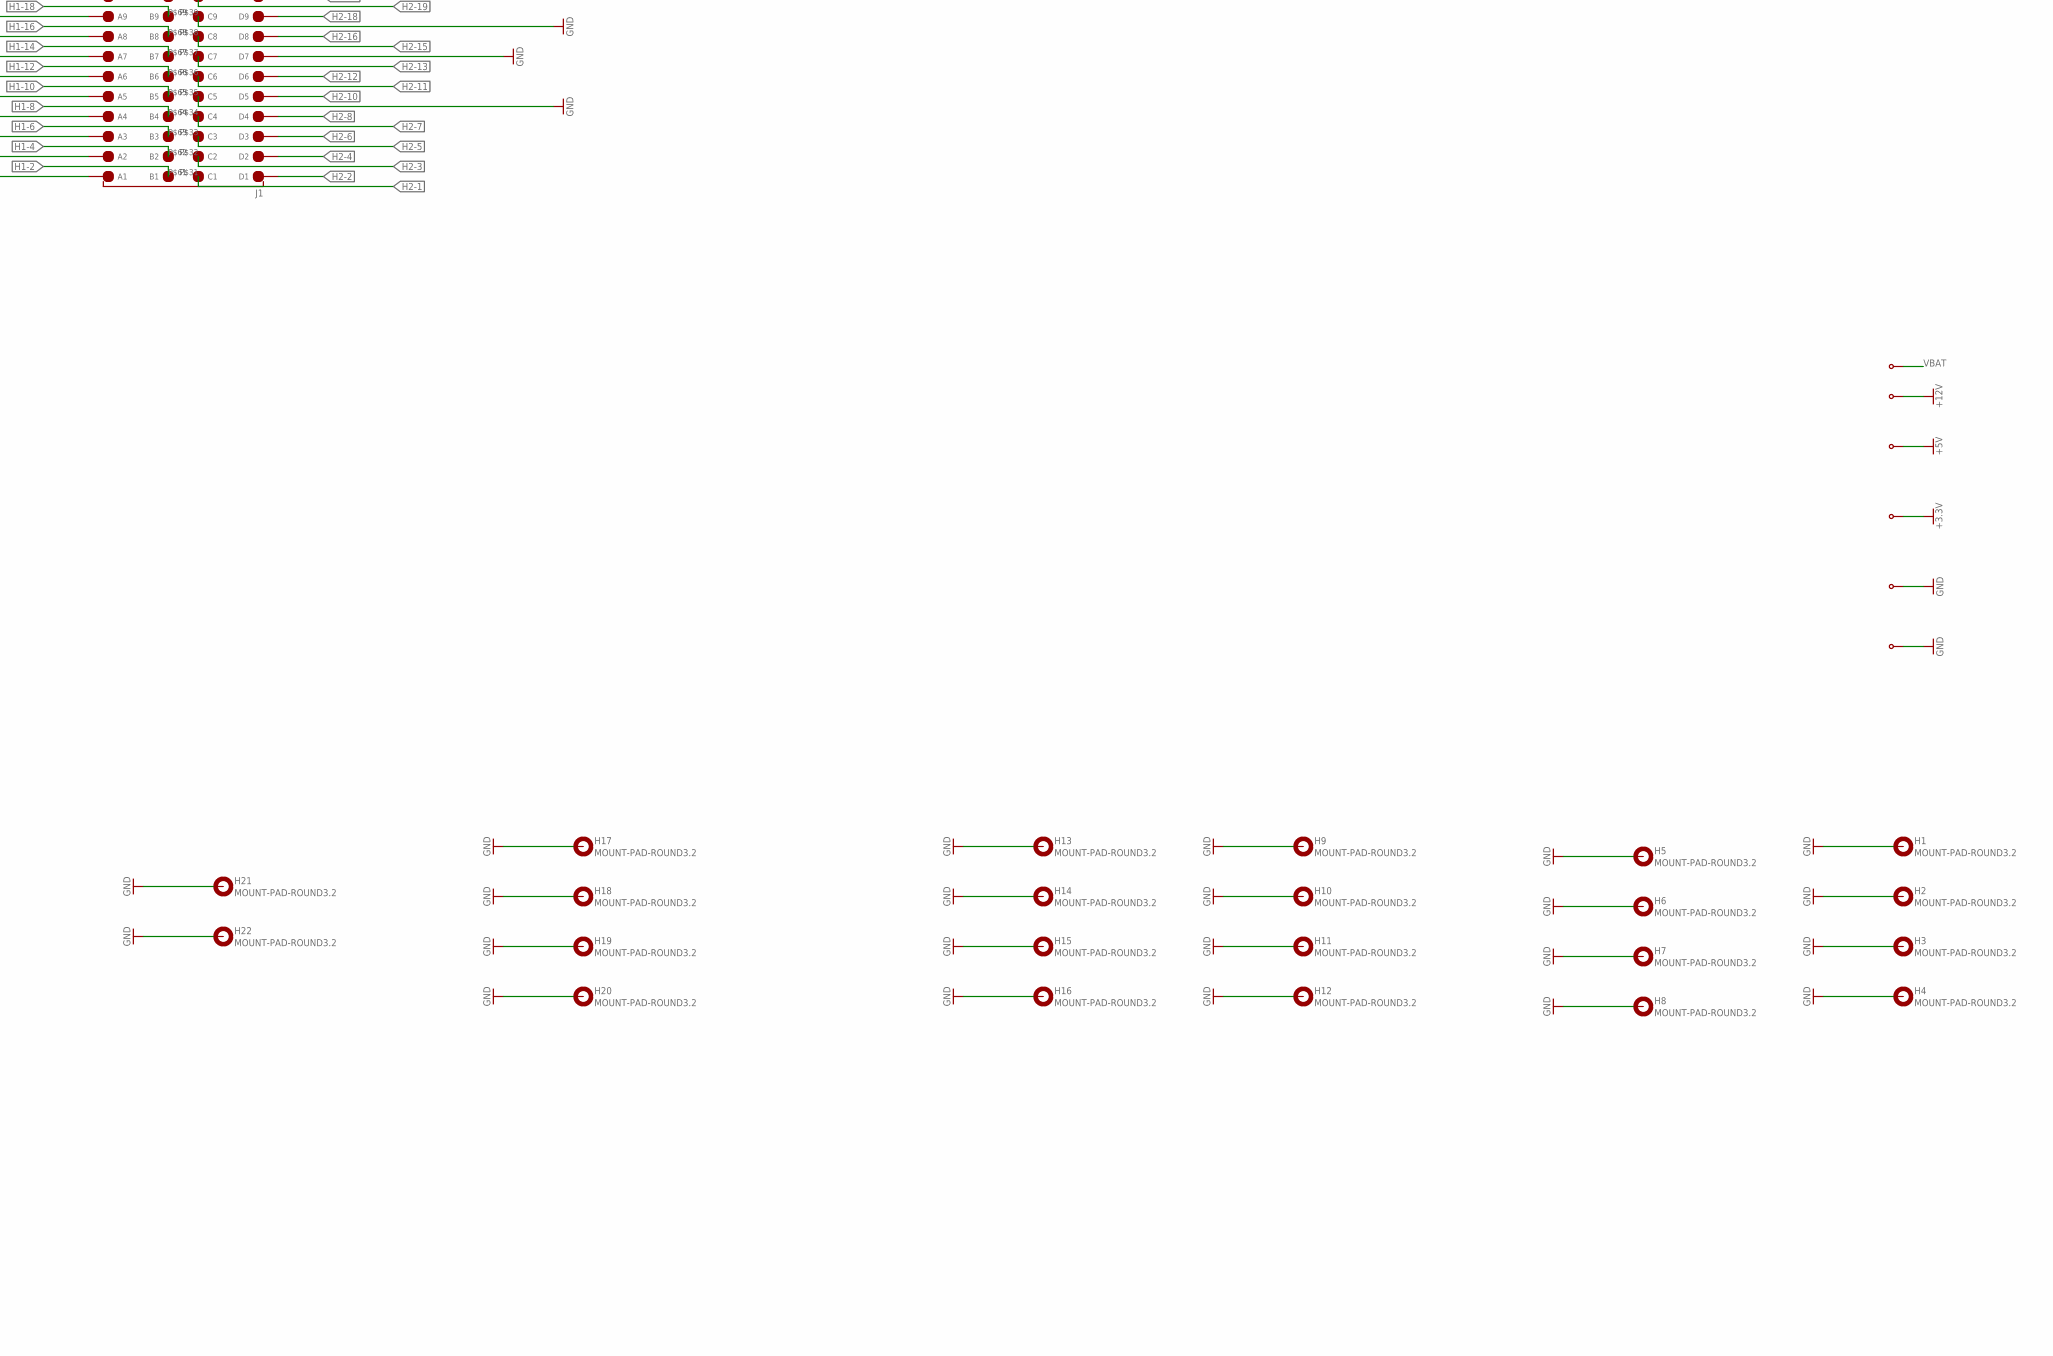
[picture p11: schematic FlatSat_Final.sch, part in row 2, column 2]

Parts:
H1, H2, H3, H4, H5, H6, H7, H8, H9, H10, H11, H12, H13, H14, H15, H16, H17, H18, H19, H20, H21, H22: MOUNT-PAD-ROUND3.2; 3,2-PAD
J1, J2, J3, J4, J5, J6: M22-6013005; RHDR120W55P200_4X30_6020X820X9
TP1, TP2, TP3, TP4, TP5, TP6, TP7, TP8, TP9, TP10, TP11, TP12: PTR1PAD1-13; P1-13
U$1, U$2, U$3, U$4, U$5, U$6: BANANA-JACK; BANANA-PRINT

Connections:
+3.3V: J1.P$14 (D14), J1.P$44 (C14), J2.P$14 (D14), J2.P$44 (C14), J3.P$14 (D14), J3.P$44 (C14), J4.P$14 (D14), J4.P$44 (C14), U$3.P$1
+5V: J1.P$13 (D13), J1.P$43 (C13), J2.P$13 (D13), J2.P$43 (C13), J3.P$13 (D13), J3.P$43 (C13), J4.P$13 (D13), J4.P$43 (C13), U$2.P$1
+12V: J1.P$12 (D12), J1.P$42 (C12), J2.P$12 (D12), J2.P$42 (C12), J3.P$12 (D12), J3.P$42 (C12), J4.P$12 (D12), J4.P$42 (C12), U$1.P$1
GND: H1.B3,2, H2.B3,2, H3.B3,2, H4.B3,2, H5.B3,2, H6.B3,2, H7.B3,2, H8.B3,2, H9.B3,2, H10.B3,2, H11.B3,2, H12.B3,2, H13.B3,2, H14.B3,2, H15.B3,2, H16.B3,2, H17.B3,2, H18.B3,2, H19.B3,2, H20.B3,2, H21.B3,2, H22.B3,2, J1.P$7 (D7), J1.P$11 (D11), J1.P$15 (D15), J1.P$16 (D16), J1.P$24 (D24), J1.P$35 (C5), J1.P$39 (C9), J1.P$41 (C11), J1.P$45 (C15), J1.P$54 (C24), J2.P$7 (D7), J2.P$11 (D11), J2.P$15 (D15), J2.P$16 (D16), J2.P$24 (D24), J2.P$35 (C5), J2.P$39 (C9), J2.P$41 (C11), J2.P$45 (C15), J2.P$54 (C24), J3.P$7 (D7), J3.P$11 (D11), J3.P$15 (D15), J3.P$16 (D16), J3.P$24 (D24), J3.P$35 (C5), J3.P$39 (C9), J3.P$41 (C11), J3.P$45 (C15), J3.P$54 (C24), J4.P$7 (D7), J4.P$11 (D11), J4.P$15 (D15), J4.P$16 (D16), J4.P$24 (D24), J4.P$35 (C5), J4.P$39 (C9), J4.P$41 (C11), J4.P$45 (C15), J4.P$54 (C24), J5.P$7 (D7), J5.P$11 (D11), J5.P$15 (D15), J5.P$16 (D16), J5.P$24 (D24), J5.P$35 (C5), J5.P$39 (C9), J5.P$41 (C11), J5.P$45 (C15), J5.P$54 (C24), J6.P$7 (D7), J6.P$11 (D11), J6.P$15 (D15), J6.P$16 (D16), J6.P$24 (D24), J6.P$35 (C5), J6.P$39 (C9), J6.P$41 (C11), J6.P$45 (C15), J6.P$54 (C24), TP1.TP, TP2.TP, TP3.TP, TP4.TP, TP5.TP, TP6.TP, TP7.TP, TP8.TP, TP9.TP, TP10.TP, TP11.TP, TP12.TP, U$4.P$1, U$5.P$1
H1-1: J1.P$91 (A1), J2.P$91 (A1), J3.P$91 (A1), J4.P$91 (A1), J5.P$91 (A1), J6.P$91 (A1)
H1-2: J1.P$61 (B1), J2.P$61 (B1), J3.P$61 (B1), J4.P$61 (B1), J5.P$61 (B1), J6.P$61 (B1)
H1-3: J1.P$92 (A2), J2.P$92 (A2), J3.P$92 (A2), J4.P$92 (A2), J5.P$92 (A2), J6.P$92 (A2)
H1-4: J1.P$62 (B2), J2.P$62 (B2), J3.P$62 (B2), J4.P$62 (B2), J5.P$62 (B2), J6.P$62 (B2)
H1-5: J1.P$93 (A3), J2.P$93 (A3), J3.P$93 (A3), J4.P$93 (A3), J5.P$93 (A3), J6.P$93 (A3)
H1-6: J1.P$63 (B3), J2.P$63 (B3), J3.P$63 (B3), J4.P$63 (B3), J5.P$63 (B3), J6.P$63 (B3)
H1-7: J1.P$94 (A4), J2.P$94 (A4), J3.P$94 (A4), J4.P$94 (A4), J5.P$94 (A4), J6.P$94 (A4)
H1-8: J1.P$64 (B4), J2.P$64 (B4), J3.P$64 (B4), J4.P$64 (B4), J5.P$64 (B4), J6.P$64 (B4)
H1-9: J1.P$95 (A5), J2.P$95 (A5), J3.P$95 (A5), J4.P$95 (A5), J5.P$95 (A5), J6.P$95 (A5)
H1-10: J1.P$65 (B5), J2.P$65 (B5), J3.P$65 (B5), J4.P$65 (B5), J5.P$65 (B5), J6.P$65 (B5)
H1-11: J1.P$96 (A6), J2.P$96 (A6), J3.P$96 (A6), J4.P$96 (A6), J5.P$96 (A6), J6.P$96 (A6)
H1-12: J1.P$66 (B6), J2.P$66 (B6), J3.P$66 (B6), J4.P$66 (B6), J5.P$66 (B6), J6.P$66 (B6)
H1-13: J1.P$97 (A7), J2.P$97 (A7), J3.P$97 (A7), J4.P$97 (A7), J5.P$97 (A7), J6.P$97 (A7)
H1-14: J1.P$67 (B7), J2.P$67 (B7), J3.P$67 (B7), J4.P$67 (B7), J5.P$67 (B7), J6.P$67 (B7)
H1-15: J1.P$98 (A8), J2.P$98 (A8), J3.P$98 (A8), J4.P$98 (A8), J5.P$98 (A8), J6.P$98 (A8)
H1-16: J1.P$68 (B8), J2.P$68 (B8), J3.P$68 (B8), J4.P$68 (B8), J5.P$68 (B8), J6.P$68 (B8)
H1-17: J1.P$99 (A9), J2.P$99 (A9), J3.P$99 (A9), J4.P$99 (A9), J5.P$99 (A9), J6.P$99 (A9)
H1-18: J1.P$69 (B9), J2.P$69 (B9), J3.P$69 (B9), J4.P$69 (B9), J5.P$69 (B9), J6.P$69 (B9)
H1-19: J1.P$100 (A10), J2.P$100 (A10), J3.P$100 (A10), J4.P$100 (A10), J5.P$100 (A10), J6.P$100 (A10)
H1-20: J1.P$70 (B10), J2.P$70 (B10), J3.P$70 (B10), J4.P$70 (B10), J5.P$70 (B10), J6.P$70 (B10)
H1-21: J1.P$101 (A11), J2.P$101 (A11), J3.P$101 (A11), J4.P$101 (A11), J5.P$101 (A11), J6.P$101 (A11)
H1-22: J1.P$71 (B11), J2.P$71 (B11), J3.P$71 (B11), J4.P$71 (B11), J5.P$71 (B11), J6.P$71 (B11)
H1-23: J1.P$102 (A12), J2.P$102 (A12), J3.P$102 (A12), J4.P$102 (A12), J5.P$102 (A12), J6.P$102 (A12)
H1-24: J1.P$72 (B12), J2.P$72 (B12), J3.P$72 (B12), J4.P$72 (B12), J5.P$72 (B12), J6.P$72 (B12)
H1-25: J1.P$103 (A13), J2.P$103 (A13), J3.P$103 (A13), J4.P$103 (A13), J5.P$103 (A13), J6.P$103 (A13)
H1-26: J1.P$73 (B13), J2.P$73 (B13), J3.P$73 (B13), J4.P$73 (B13), J5.P$73 (B13), J6.P$73 (B13)
H1-27: J1.P$104 (A14), J2.P$104 (A14), J3.P$104 (A14), J4.P$104 (A14), J5.P$104 (A14), J6.P$104 (A14)
H1-28: J1.P$74 (B14), J2.P$74 (B14), J3.P$74 (B14), J4.P$74 (B14), J5.P$74 (B14), J6.P$74 (B14)
H1-29: J1.P$105 (A15), J2.P$105 (A15), J3.P$105 (A15), J4.P$105 (A15), J5.P$105 (A15), J6.P$105 (A15)
H1-30: J1.P$75 (B15), J2.P$75 (B15), J3.P$75 (B15), J4.P$75 (B15), J5.P$75 (B15), J6.P$75 (B15)
H1-31: J1.P$106 (A16), J2.P$106 (A16), J3.P$106 (A16), J4.P$106 (A16), J5.P$106 (A16), J6.P$106 (A16)
H1-32: J1.P$76 (B16), J2.P$76 (B16), J3.P$76 (B16), J4.P$76 (B16), J5.P$76 (B16), J6.P$76 (B16)
H1-33: J1.P$107 (A17), J2.P$107 (A17), J3.P$107 (A17), J4.P$107 (A17), J5.P$107 (A17), J6.P$107 (A17)
H1-34: J1.P$77 (B17), J2.P$77 (B17), J3.P$77 (B17), J4.P$77 (B17), J5.P$77 (B17), J6.P$77 (B17)
H1-35: J1.P$108 (A18), J2.P$108 (A18), J3.P$108 (A18), J4.P$108 (A18), J5.P$108 (A18), J6.P$108 (A18)
H1-36: J1.P$78 (B18), J2.P$78 (B18), J3.P$78 (B18), J4.P$78 (B18), J5.P$78 (B18), J6.P$78 (B18)
H1-37: J1.P$109 (A19), J2.P$109 (A19), J3.P$109 (A19), J4.P$109 (A19), J5.P$109 (A19), J6.P$109 (A19)
H1-38: J1.P$79 (B19), J2.P$79 (B19), J3.P$79 (B19), J4.P$79 (B19), J5.P$79 (B19), J6.P$79 (B19)
H1-39: J1.P$110 (A20), J2.P$110 (A20), J3.P$110 (A20), J4.P$110 (A20), J5.P$110 (A20), J6.P$110 (A20)
H1-40: J1.P$80 (B20), J2.P$80 (B20), J3.P$80 (B20), J4.P$80 (B20), J5.P$80 (B20), J6.P$80 (B20)
H1-41: J1.P$111 (A21), J2.P$111 (A21), J3.P$111 (A21), J4.P$111 (A21), J5.P$111 (A21), J6.P$111 (A21)
H1-42: J1.P$81 (B21), J2.P$81 (B21), J3.P$81 (B21), J4.P$81 (B21), J5.P$81 (B21), J6.P$81 (B21)
H1-43: J1.P$112 (A22), J2.P$112 (A22), J3.P$112 (A22), J4.P$112 (A22), J5.P$112 (A22), J6.P$112 (A22)
H1-44: J1.P$82 (B22), J2.P$82 (B22), J3.P$82 (B22), J4.P$82 (B22), J5.P$82 (B22), J6.P$82 (B22)
H1-45: J1.P$113 (A23), J2.P$113 (A23), J3.P$113 (A23), J4.P$113 (A23), J5.P$113 (A23), J6.P$113 (A23)
H1-46: J1.P$83 (B23), J2.P$83 (B23), J3.P$83 (B23), J4.P$83 (B23), J5.P$83 (B23), J6.P$83 (B23)
H1-47: J1.P$114 (A24), J2.P$114 (A24), J3.P$114 (A24), J4.P$114 (A24), J5.P$114 (A24), J6.P$114 (A24)
H1-48: J1.P$84 (B24), J2.P$84 (B24), J3.P$84 (B24), J4.P$84 (B24), J5.P$84 (B24), J6.P$84 (B24)
H1-49: J1.P$115 (A25), J2.P$115 (A25), J3.P$115 (A25), J4.P$115 (A25), J5.P$115 (A25), J6.P$115 (A25)
H1-50: J1.P$85 (B25), J2.P$85 (B25), J3.P$85 (B25), J4.P$85 (B25), J5.P$85 (B25), J6.P$85 (B25)
H1-51: J1.P$116 (A26), J2.P$116 (A26), J3.P$116 (A26), J4.P$116 (A26), J5.P$116 (A26), J6.P$116 (A26)
H1-52: J1.P$86 (B26), J2.P$86 (B26), J3.P$86 (B26), J4.P$86 (B26), J5.P$86 (B26), J6.P$86 (B26)
H2-1: J1.P$31 (C1), J2.P$31 (C1), J3.P$31 (C1), J4.P$31 (C1), J5.P$31 (C1), J6.P$31 (C1)
H2-2: J1.P$1 (D1), J2.P$1 (D1), J3.P$1 (D1), J4.P$1 (D1), J5.P$1 (D1), J6.P$1 (D1)
H2-3: J1.P$32 (C2), J2.P$32 (C2), J3.P$32 (C2), J4.P$32 (C2), J5.P$32 (C2), J6.P$32 (C2)
H2-4: J1.P$2 (D2), J2.P$2 (D2), J3.P$2 (D2), J4.P$2 (D2), J5.P$2 (D2), J6.P$2 (D2)
H2-5: J1.P$33 (C3), J2.P$33 (C3), J3.P$33 (C3), J4.P$33 (C3), J5.P$33 (C3), J6.P$33 (C3)
H2-6: J1.P$3 (D3), J2.P$3 (D3), J3.P$3 (D3), J4.P$3 (D3), J5.P$3 (D3), J6.P$3 (D3)
H2-7: J1.P$34 (C4), J2.P$34 (C4), J3.P$34 (C4), J4.P$34 (C4), J5.P$34 (C4), J6.P$34 (C4)
H2-8: J1.P$4 (D4), J2.P$4 (D4), J3.P$4 (D4), J4.P$4 (D4), J5.P$4 (D4), J6.P$4 (D4)
H2-10: J1.P$5 (D5), J2.P$5 (D5), J3.P$5 (D5), J4.P$5 (D5), J5.P$5 (D5), J6.P$5 (D5)
H2-11: J1.P$36 (C6), J2.P$36 (C6), J3.P$36 (C6), J4.P$36 (C6), J5.P$36 (C6), J6.P$36 (C6)
H2-12: J1.P$6 (D6), J2.P$6 (D6), J3.P$6 (D6), J4.P$6 (D6), J5.P$6 (D6), J6.P$6 (D6)
H2-13: J1.P$37 (C7), J2.P$37 (C7), J3.P$37 (C7), J4.P$37 (C7), J5.P$37 (C7), J6.P$37 (C7)
H2-15: J1.P$38 (C8), J2.P$38 (C8), J3.P$38 (C8), J4.P$38 (C8), J5.P$38 (C8), J6.P$38 (C8)
H2-16: J1.P$8 (D8), J2.P$8 (D8), J3.P$8 (D8), J4.P$8 (D8), J5.P$8 (D8), J6.P$8 (D8)
H2-18: J1.P$9 (D9), J2.P$9 (D9), J3.P$9 (D9), J4.P$9 (D9), J5.P$9 (D9), J6.P$9 (D9)
H2-19: J1.P$40 (C10), J2.P$40 (C10), J3.P$40 (C10), J4.P$40 (C10), J5.P$40 (C10), J6.P$40 (C10)
H2-20: J1.P$10 (D10), J2.P$10 (D10), J3.P$10 (D10), J4.P$10 (D10), J5.P$10 (D10), J6.P$10 (D10)
H2-31: J1.P$46 (C16), J2.P$46 (C16), J3.P$46 (C16), J4.P$46 (C16), J5.P$46 (C16), J6.P$46 (C16)
H2-33: J1.P$47 (C17), J2.P$47 (C17), J3.P$47 (C17), J4.P$47 (C17), J5.P$47 (C17), J6.P$47 (C17)
H2-34: J1.P$17 (D17), J2.P$17 (D17), J3.P$17 (D17), J4.P$17 (D17), J5.P$17 (D17), J6.P$17 (D17)
H2-35: J1.P$48 (C18), J2.P$48 (C18), J3.P$48 (C18), J4.P$48 (C18), J5.P$48 (C18), J6.P$48 (C18)
H2-36: J1.P$18 (D18), J2.P$18 (D18), J3.P$18 (D18), J4.P$18 (D18), J5.P$18 (D18), J6.P$18 (D18)
H2-37: J1.P$49 (C19), J2.P$49 (C19), J3.P$49 (C19), J4.P$49 (C19), J5.P$49 (C19), J6.P$49 (C19)
H2-38: J1.P$19 (D19), J2.P$19 (D19), J3.P$19 (D19), J4.P$19 (D19), J5.P$19 (D19), J6.P$19 (D19)
H2-39: J1.P$50 (C20), J2.P$50 (C20), J3.P$50 (C20), J4.P$50 (C20), J5.P$50 (C20), J6.P$50 (C20)
H2-40: J1.P$20 (D20), J2.P$20 (D20), J3.P$20 (D20), J4.P$20 (D20), J5.P$20 (D20), J6.P$20 (D20)
H2-41: J1.P$51 (C21), J2.P$51 (C21), J3.P$51 (C21), J4.P$51 (C21), J5.P$51 (C21), J6.P$51 (C21)
H2-42: J1.P$21 (D21), J2.P$21 (D21), J3.P$21 (D21), J4.P$21 (D21), J5.P$21 (D21), J6.P$21 (D21)
H2-43: J1.P$52 (C22), J2.P$52 (C22), J3.P$52 (C22), J4.P$52 (C22), J5.P$52 (C22), J6.P$52 (C22)
H2-44: J1.P$22 (D22), J2.P$22 (D22), J3.P$22 (D22), J4.P$22 (D22), J5.P$22 (D22), J6.P$22 (D22)
H2-49: J1.P$55 (C25), J2.P$55 (C25), J3.P$55 (C25), J4.P$55 (C25), J5.P$55 (C25), J6.P$55 (C25)
H2-50: J1.P$25 (D25), J2.P$25 (D25), J3.P$25 (D25), J4.P$25 (D25), J5.P$25 (D25), J6.P$25 (D25)
H2-51: J1.P$56 (C26), J2.P$56 (C26), J3.P$56 (C26), J4.P$56 (C26), J5.P$56 (C26), J6.P$56 (C26)
H2-52: J1.P$26 (D26), J2.P$26 (D26), J3.P$26 (D26), J4.P$26 (D26), J5.P$26 (D26), J6.P$26 (D26)
UN01: J1.P$117 (A27), J2.P$117 (A27), J3.P$117 (A27), J4.P$117 (A27), J5.P$117 (A27), J6.P$117 (A27)
UN02: J1.P$87 (B27), J2.P$87 (B27), J3.P$87 (B27), J4.P$87 (B27), J5.P$87 (B27), J6.P$87 (B27)
UN03: J1.P$118 (A28), J2.P$118 (A28), J3.P$118 (A28), J4.P$118 (A28), J5.P$118 (A28), J6.P$118 (A28)
UN04: J1.P$88 (B28), J2.P$88 (B28), J3.P$88 (B28), J4.P$88 (B28), J5.P$88 (B28), J6.P$88 (B28)
UN05: J1.P$119 (A29), J2.P$119 (A29), J3.P$119 (A29), J4.P$119 (A29), J5.P$119 (A29), J6.P$119 (A29)
UN06: J1.P$89 (B29), J2.P$89 (B29), J3.P$89 (B29), J4.P$89 (B29), J5.P$89 (B29), J6.P$89 (B29)
UN07: J1.P$120 (A30), J2.P$120 (A30), J3.P$120 (A30), J4.P$120 (A30), J5.P$120 (A30), J6.P$120 (A30)
UN08: J1.P$90 (B30), J2.P$90 (B30), J3.P$90 (B30), J4.P$90 (B30), J5.P$90 (B30), J6.P$90 (B30)
UN09: J1.P$57 (C27), J2.P$57 (C27), J3.P$57 (C27), J4.P$57 (C27), J5.P$57 (C27), J6.P$57 (C27)
UN10: J1.P$27 (D27), J2.P$27 (D27), J3.P$27 (D27), J4.P$27 (D27), J5.P$27 (D27), J6.P$27 (D27)
UN11: J1.P$58 (C28), J2.P$58 (C28), J3.P$58 (C28), J4.P$58 (C28), J5.P$58 (C28), J6.P$58 (C28)
UN12: J1.P$28 (D28), J2.P$28 (D28), J3.P$28 (D28), J4.P$28 (D28), J5.P$28 (D28), J6.P$28 (D28)
UN13: J1.P$59 (C29), J2.P$59 (C29), J3.P$59 (C29), J4.P$59 (C29), J5.P$59 (C29), J6.P$59 (C29)
UN14: J1.P$29 (D29), J2.P$29 (D29), J3.P$29 (D29), J4.P$29 (D29), J5.P$29 (D29), J6.P$29 (D29)
UN15: J1.P$60 (C30), J2.P$60 (C30), J3.P$60 (C30), J4.P$60 (C30), J5.P$60 (C30), J6.P$60 (C30)
UN16: J1.P$30 (D30), J2.P$30 (D30), J3.P$30 (D30), J4.P$30 (D30), J5.P$30 (D30), J6.P$30 (D30)
VBAT: J1.P$23 (D23), J1.P$53 (C23), J2.P$23 (D23), J2.P$53 (C23), J3.P$23 (D23), J3.P$53 (C23), J4.P$23 (D23), J4.P$53 (C23), U$6.P$1

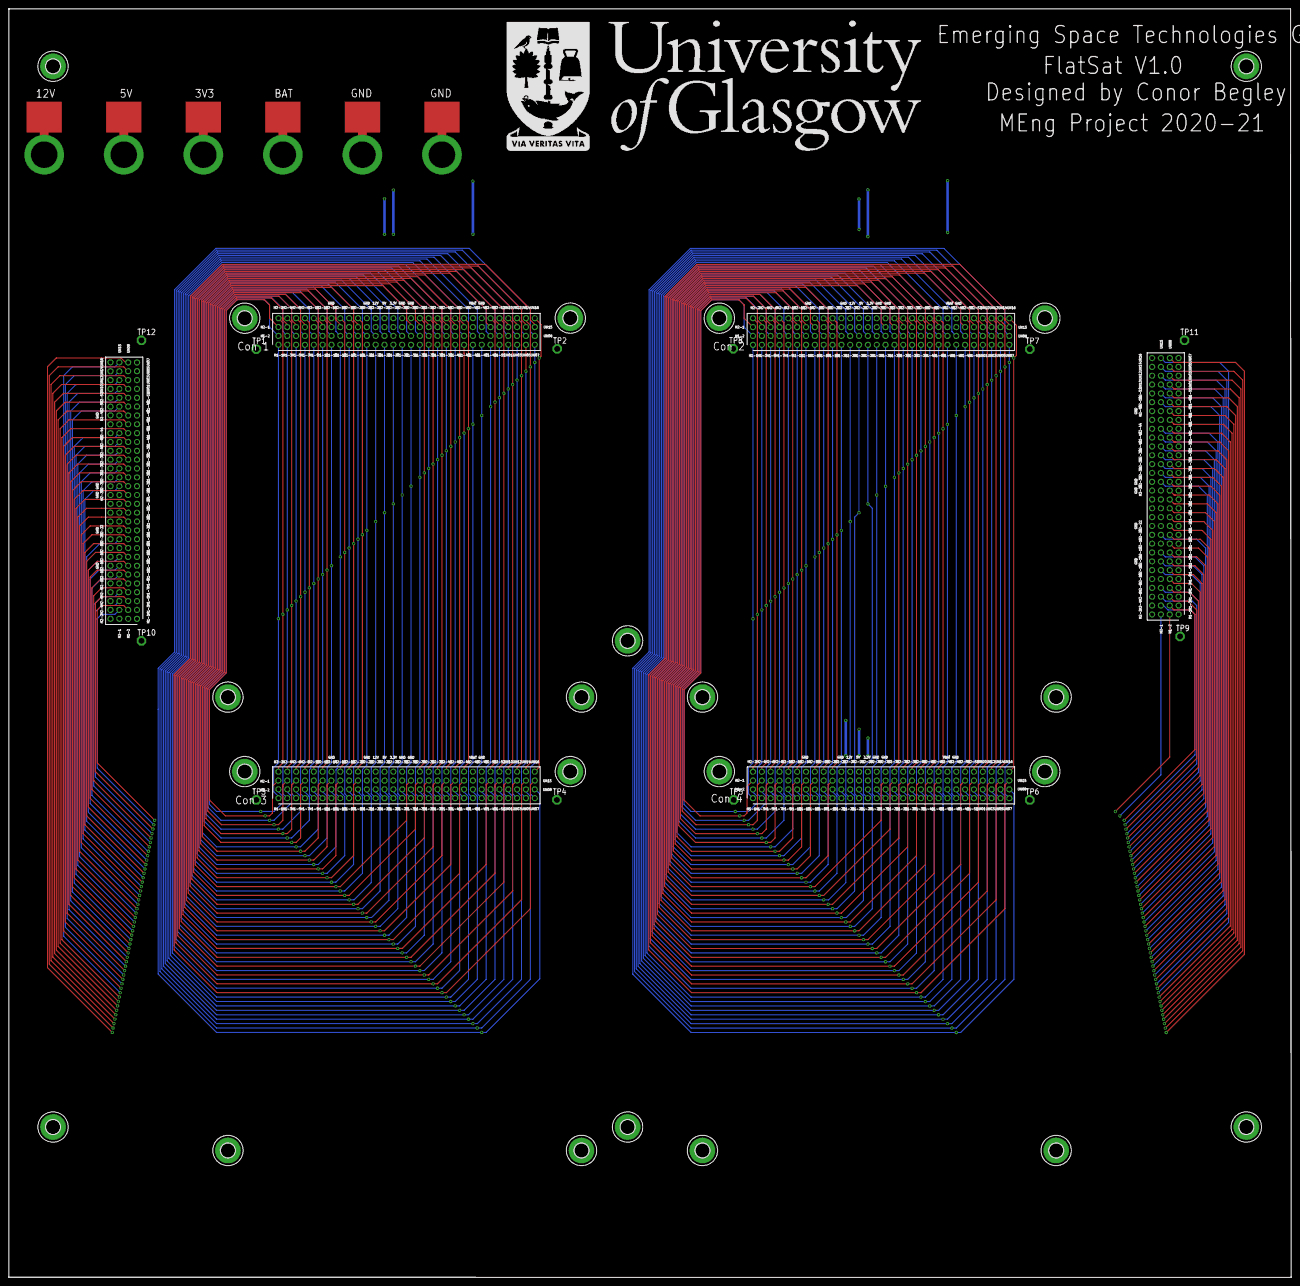
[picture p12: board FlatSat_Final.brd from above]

Board: 4 copper layers, 290.1 x 287.0 mm, 46 parts (0 on the bottom side), 107 nets.

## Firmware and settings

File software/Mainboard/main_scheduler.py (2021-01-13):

import mono_sch as sch
import com as com
import time
import os
import sys
from pins import pins
import digitalio
import json
import custom_functions as cf
import interrupt_functions as intrf

class scheduler():
    def __init__(self, buffer_size = None, buffer=None, increment=1):
        if buffer:
            self.buffer = buffer
            self.buffer_size = len(buffer)
        elif buffer_size:
            self.buffer = bytearray(buffer_size)
            self.buffer_size = buffer_size
        else:
            self.buffer = bytearray(0)
            self.buffer_size = 0
        self.increment = increment
        self.task_pattern = None
        self.sch_period = None

    def run_SPI(self, task, data):
        res = None

        if task["connection"]["receive"] or task["connection"]["send"]:
            res = com.Com_SPI(
                data_size = task["connection"]["data_size"],
                data = data,
                delimiter = task["connection"]["data_delimiter"],
                start = task["connection_settings"]["start"],
                start_value = task["connection_settings"]["start_value"],
                end = task["connection_settings"]["end"],
                end_value = task["connection_settings"]["end_value"],
                front_data_padding = task["connection_settings"]["front_data_padding"],
                back_data_padding = task["connection_settings"]["back_data_padding"],
                baud = self.devices[task["connection"]["device_name"]]["SPI"]["baud"],
                bits = self.devices[task["connection"]["device_name"]]["SPI"]["bits"],
                polarity = self.devices[task["connection"]["device_name"]]["SPI"]["polarity"],
                phase = self.devices[task["connection"]["device_name"]]["SPI"]["phase"],
                write_value = self.devices[task["connection"]["device_name"]]["SPI"]["write_value"],
                CLK = pins[self.devices[task["connection"]["device_name"]]["SPI"]["CLK"]],
                MOSI = pins[self.devices[task["connection"]["device_name"]]["SPI"]["MOSI"]],
                MISO = pins[self.devices[task["connection"]["device_name"]]["SPI"]["MISO"]],
                )

            if res != None:
                if task["connection"]["pass_through"]:
                    com.Com_SPI(
                        data = res,
                        delimiter = task["connection"]["data_delimiter"],
                        start = task["connection_settings"]["start"],
                        start_value = task["connection_settings"]["start_value"],
                        end = task["connection_settings"]["end"],
                        end_value = task["connection_settings"]["end_value"],
                        front_data_padding = task["connection_settings"]["front_data_padding"],
                        back_data_padding = task["connection_settings"]["back_data_padding"],
                        baud = self.devices[task["connection"]["device_name"]]["SPI"]["baud"],
                        bits = self.devices[task["connection"]["device_name"]]["SPI"]["bits"],
                        polarity = self.devices[task["connection"]["device_name"]]["SPI"]["polarity"],
                        phase = self.devices[task["connection"]["device_name"]]["SPI"]["phase"],
                        write_value = self.devices[task["connection"]["device_name"]]["SPI"]["write_value"],
                        CLK = pins[self.devices[task["connection"]["device_name"]]["SPI"]["CLK"]],
                        MOSI = pins[self.devices[task["connection"]["device_name"]]["SPI"]["MOSI"]],
                        MISO = pins[self.devices[task["connection"]["device_name"]]["SPI"]["MISO"]],
                        )
        return res

    def run_UART(self, task, data):
        res = None

        if task["connection"]["receive"] or task["connection"]["send"]:
            res = com.Com_UART(
                        data_size = task["connection"]["data_size"],
                        data = data,
                        delimiter = task["connection"]["data_delimiter"],
                        start = task["connection_settings"]["start"],
                        start_value = task["connection_settings"]["start_value"],
                        end = task["connection_settings"]["end"],
                        end_value = task["connection_settings"]["end_value"],
                        front_data_padding = task["connection_settings"]["front_data_padding"],
                        back_data_padding = task["connection_settings"]["back_data_padding"],
                        baud = self.devices[task["connection"]["device_name"]]["UART"]["baud"],
                        bits = self.devices[task["connection"]["device_name"]]["UART"]["bits"],
                        parity = self.devices[task["connection"]["device_name"]]["UART"]["parity"],
                        stop = self.devices[task["connection"]["device_name"]]["UART"]["stop"],
                        timeout = self.devices[task["connection"]["device_name"]]["UART"]["timeout"],
                        receiver_buffer_size = self.devices[task["connection"]["device_name"]]["UART"]["receiver_buffer_size"],
                        TX = pins[self.devices[task["connection"]["device_name"]]["UART"]["TX"]],
                        RX = pins[self.devices[task["connection"]["device_name"]]["UART"]["RX"]]
                  )

            if res != None:
                if task["connection"]["pass_through"]:
                    res = com.Com_UART(
                        data = res,
                        delimiter = task["connection"]["data_delimiter"],
                        front_data_padding = task["connection_settings"]["front_data_padding"],
                        back_data_padding = task["connection_settings"]["back_data_padding"],
                        start = task["connection_settings"]["start"],
                        start_value = task["connection_settings"]["start_value"],
                        end = task["connection_settings"]["end"],
                        end_value = task["connection_settings"]["end_value"],
                        baud = self.devices[task["connection"]["pass_location"]]["UART"]["baud"],
                        bits = self.devices[task["connection"]["pass_location"]]["UART"]["bits"],
                        parity = self.devices[task["connection"]["pass_location"]]["UART"]["parity"],
                        stop = self.devices[task["connection"]["pass_location"]]["UART"]["stop"],
                        timeout = self.devices[task["connection"]["pass_location"]]["UART"]["timeout"],
                        receiver_buffer_size = self.devices[task["connection"]["pass_location"]]["UART"]["receiver_buffer_size"],
                        TX = pins[self.devices[task["connection"]["pass_location"]]["UART"]["TX"]],
                        RX = pins[self.devices[task["connection"]["pass_location"]]["UART"]["RX"]]
                    )
        return res

    def run_I2C(self, task, data):
        res = None

        if task["connection"]["receive"] or task["connection"]["send"]:
            res = com.Com_I2C(
                self.devices[task["connection"]["device_name"]]["I2C"]["address"],
                data_size = task["connection"]["data_size"],
                data = data,
                delimiter = task["connection"]["data_delimiter"],
                start = task["connection_settings"]["start"],
                start_value = task["connection_settings"]["start_value"],
                end = task["connection_settings"]["end"],
                end_value = task["connection_settings"]["end_value"],
                front_data_padding = task["connection_settings"]["front_data_padding"],
                back_data_padding = task["connection_settings"]["back_data_padding"],
                SDA= pins[self.devices[task["connection"]["device_name"]]["I2C"]["SDA"]],
                SCL= pins[self.devices[task["connection"]["device_name"]]["I2C"]["SCL"]],
                frequency = self.devices[task["connection"]["device_name"]]["I2C"]["frequency"]
                )

            if res != None:
                if task["connection"]["pass_through"]:
                    com.Com_I2C(devices[task["connection"]["pass_location"]]["I2C"]["address"],
                    data = res,
                    delimiter = task["connection"]["data_delimiter"],
                    front_data_padding = task["connection_settings"]["front_data_padding"],
                    back_data_padding = task["connection_settings"]["back_data_padding"],
                    start=task["connection_settings"]["start"],
                    start_value = task["connection_settings"]["start_value"],
                    end=task["connection_settings"]["end"],
                    end_value = task["connection_settings"]["end_value"],
                    SDA= pins[devices[task["connection"]["pass_location"]]["I2C"]["SDA"]],
                    SCL= pins[devices[task["connection"]["pass_location"]]["I2C"]["SCL"]],
                    frequency = devices[task["connection"]["pass_location"]]["I2C"]["baud"]
                    )
        return res

    def handle_interrupt(self, task):
        intr_pins = []
        for pin in task["pins"]:
             p = digitalio.DigitalInOut(pins[pin])
             p.switch_to_input()
             intr_pins.append(p)
        intrf.func_dict[task["interrupt_function"]](self.buffer,self.devices, intr_pins,task["arguments"])

        for pin in intr_pins:
            pin.deinit()

    def setup(self,base_folder = "", tasks_folder = "tasks/", devices_folder ="devices/", interrupts_folder  = "interrupts/",
              schedule= None, devices = "devices.txt", default_task="default_task.txt",
              default_device="default_devices.txt", default_interrupt = "default_interrupt.txt", step=1, margin = 0.2):

        interrupt_files = os.listdir(base_folder+interrupts_folder)
        task_files = os.listdir(base_folder+tasks_folder)
        if default_task in task_files:
                    task_files.remove(default_task)

        if default_interrupt in interrupt_files:
            interrupt_files.remove(default_interrupt)

        self.tasks = {}
        self.devices = {}

        with open(base_folder + devices_folder + devices) as f:
            self.devices = json.loads(f.read())

        with open(base_folder + devices_folder+default_device) as f:
            devices_default = json.loads(f.read())

            for device in self.devices:
                self.devices[device] = com.add_default_dict(self.devices[device], devices_default)

        with open(base_folder + interrupts_folder + default_interrupt) as f:
            interrupt_default = json.loads(f.read())
            for file in interrupt_files:
                with open(base_folder+interrupts_folder+file) as f:
                    interrupts = json.loads(f.read())
                    for interrupt in interrupts:
                        self.tasks[interrupt] = com.add_default_dict(interrupts[interrupt], interrupt_default)
                        self.tasks[interrupt]["task_type"] = "interrupt"

        with open(base_folder + tasks_folder+default_task) as f:
            tasks_default = json.loads(f.read())

            for file in task_files:
                with open(base_folder + tasks_folder+ file) as f:
                    tasks = json.loads(f.read())
                    for task in tasks:
                        if "duration" in tasks[task]:
                            if tasks[task]["duration"] == "estimate":
                                tasks[task]["duration"] = com.calculate_duration(tasks[task], self.devices, margin=margin)
                            elif tasks[task]["duration"] == "run":
                                tasks[task]["duration"] = self.calculate_run(tasks[task], margin=margin)
                        self.tasks[task] = com.add_default_dict(tasks[task], tasks_default)
                        self.tasks[task]["task_type"] = "task"

        if schedule == None:
            if not sch.possible_schedule(self.tasks):
                return False

            self.task_pattern, self.sch_period = sch.schedule_order(self.tasks, step=step)
        else:
            self.task_pattern, self.sch_period = schedule[0], schedule[1]
        return True

    def run_task(self,task_name):
        task = self.tasks[task_name]
        self.task_run(task)

    def task_run(self, task):
        active_pins = []

        if task["task_type"] == "interrupt":
            self.handle_interrupt(task)
        else:
            #Set pins high and low
            if "pins" in task:
                for pin in task["pins"]["pin_high"]:
                    p = digitalio.DigitalInOut(pins[pin])
                    p.direction = digitalio.Direction.OUTPUT
                    p.value = True
                    active_pins.append(p)

                for pin in task["pins"]["pin_low"]:
                    p = digitalio.DigitalInOut(pins[pin])
                    p.direction = digitalio.Direction.OUTPUT
                    p.value = False
                    active_pins.append(p)

            data = task["connection"]["data"]
            #Load data
            if task["load_settings"]["load_from_buf"]:
                data = self.buffer[task["load_settings"]["load_address_start"]:task["load_settings"]["load_address_end"]]

            if task["load_settings"]["load_from_file"]:
                i = 0
                lines = []
                with open(task["load_settings"]["load_file"]) as f:
                    if not task["load_settings"]["disjoint"]:
                        i = task["load_settings"]["start_line"]
                        while(i < task["load_settings"]["end_line"]):
                            lines.append(f.readline())
                            i +=1
                    else:
                        current_l = 0
                        l = task["load_settings"]["lines"][current_l]
                        while (i <= task["load_settings"]["lines"][-1]):
                            if l == i:
                                lines.append(f.readline().strip())
                                current_l += 1
                                if current_l >= len(task["load_settings"]["lines"]):
                                    break
                                l = task["load_settings"]["lines"][current_l]
                            else:
                                f.readline()
                            i += 1
                data = task["load_settings"]["line_delimiter"].join(lines)

            if task["custom_function"]["custom"] and task["custom_function"]["before"]:
                d = cf.func_dict[task["custom_function"]["custom_function_name"]](self.buffer,active_pins,data,task["custom_function"]["arguments"])
                if d != None:
                    data = d

            #Run task
            if task["connection"]["type"] == "I2C":
                data = self.run_I2C(task,data)
            elif task["connection"]["type"] == "UART":
                data = self.run_UART(task, data)
            elif task["connection"]["type"] == "SPI":
                data = self.run_SPI(task, data)
            elif task["connection"]["type"] == "CAN":
                print("CAN not implemented")
            else:
                print("Unknown connection type {}".format(task["connection"]["type"]))
            if task["custom_function"]["custom"] and task["custom_function"]["after"]:
                data = cf.func_dict[task["custom_function"]["custom_function_name"]](self.buffer,active_pins,data,task["custom_function"]["arguments"] )

            #Store data
            if task["store_settings"]["store_to_buf"]:
                addr = int(task["store_settings"]["store_address"])
                if data != None:
                    for i in range(len(data)):
                        self.buffer[addr] = data[i]
                        addr += 1
                        if addr >= self.buffer_size:
                            print("Storage overflow")
                            break

            elif task["store_settings"]["store_to_file"]:
                if task["store_settings"]["file_append"]:
                    with open(task["store_settings"]["store_file"], "a") as f:
                        f.write(data)
                        f.write("\n")
                else:
                    with open(task["store_settings"]["store_file"], "w") as f:
                        f.write(data)

            for pin in active_pins:
                pin.deinit()

    def run_schedule(self, catch_err = True):
        sch_t = -1
        i =0
        if self.task_pattern[-1] != ("end", float("inf")):
            self.task_pattern.append(("end", float("inf")))

        n = len(self.task_pattern)
        print(self.task_pattern)
        t = time.monotonic_ns()-self.increment

        while True:
                if t + self.increment <= time.monotonic_ns():
                    sch_t = (sch_t+((time.monotonic_ns()-t)//self.increment))

                    if sch_t >= self.sch_period:
                        print("Reset at {}".format(sch_t))
                        sch_t = (sch_t%self.sch_period) - 1
                        i = 0

                    t = time.monotonic_ns()
                    if self.task_pattern[i][1] <= sch_t:
                        print("Running Task {} at {}".format(self.task_pattern[i][0], sch_t))
                        try:
                            self.run_task(self.task_pattern[i][0])
                        except Exception as e:
                            if catch_err == True:
                                print("Task failed {}".format(self.task_pattern[i][0]))
                                sys.print_exception(e)
                            else:
                                raise e

                        i = ((i+1)%n)

    def run_startup(self, schedule_file = "schedule.txt", base_folder = "", startup_folder = "startup/", tasks = "tasks/"):
        self.setup(base_folder = base_folder,  tasks_folder = startup_folder + tasks, schedule = ([],[]))
        with open(base_folder+ startup_folder+ schedule_file) as f:
            lines=f.readlines()
            for line in lines:
                line = line.strip()
                self.run_task(line)
        self.devices = None
        self.task_pattern = None
        self.sch_period = None

    def calculate_run(self, task, margin = 0.2):
        t1 = time.monotonic_ns()
        try:
            self.task_run(task)
        except:
            print("Error running task, estimating duration instead")
            return com.calculate_duration(tasks[task], self.devices)
        t2 = time.monotonic_ns()
        duration = t1-t2
        duration = (1+margin) * duration
        return duration



def testing():
    global com
    import testing.mock_com as com
    global cf
    import testing.mock_custom_functions as cf
    global intrf
    import testing.mock_interrupt_functions as intrf

def undo_testing():
    global com
    import com as com
    global cf
    import custom_functions as cf
    global intrf
    import interrupt_functions as intrf



#import main_sch as m;d,s,p = m.single_setup("config.txt", [[("read_sensor", 0)], 100000]);m.run_schedule(d,s,p)
#m.run_task(d["tasks"]["read_sensor"], d["devices"]);
#import main_sch as m;d,s,p = m.setup("Case_1/", schedule=[[("read_sensor", 0)], 300000]);m.run_schedule(d,s,p)
#import main_sch as m;d,s,p = m.setup("Case_2/", schedule=[[("read_sensor", 0),("write_screen", 100000)], 300000]);m.run_schedule(d,s,p)
#import main_sch as m;d,s,p = m.setup("Case_3/", schedule=[[("read_sensor", 0),("write_screen", 100000)], 300000]);m.run_schedule(d,s,p)
#import main_sch as m;d,s,p = m.setup("Case_3/", schedule=[[("read_sensor", 0),("write_screen", 100000)], 300000]);m.run_schedule(d,s,p)
#import main_sch as m;d,s,p = m.setup("Case_3/",step=1000);m.run_schedule(d,s,p)
#import main_sch as m;d,s,p = m.setup("Case_4/", step=1000);m.run_schedule(d,s,p)
#import main_sch as m;d,s,p = m.setup("Case_5/", step=1000);m.run_schedule(d,s,p)
#import main_sch as m;d,s,p = m.setup("Case_6/", step=1000);m.run_schedule(d,s,p)
#import main_sch as m;d,s,p = m.setup("Case_7/", step=1000);m.run_schedule(d,s,p)
#import main_sch as m;d,s,p = m.setup("Demo/", step=1000);m.run_schedule(d,s,p)
#import os; os.listdir("/"); os.rename("/boot.py", "/boot.bak")

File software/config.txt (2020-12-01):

{ 
 "devices": {
                 "Coms" : {"I2C":32},
                 "Payload" : {"I2C":33}
  },
  "tasks":{
           "read_sensor":{
                          "deadline" : "Soft",                             
                          "duration": 1000000,
                          "period":   3000000,
                          "connection" :{
                                         "device_name":"Payload",
                                         "type": "I2C",
                                         "send" : false,
                                         "data" : "",
                                         "recieve": true,
                                         "data_size" : 2,
                                         "pass_through" : true,
                                         "pass_location" : "Coms"
                          },
                          "connection_settings" : {
                                                 "front_data_padding" : 1,
                                                 "back_data_padding" : 0,
                                                 "start": true,
                                                 "start_value": 0,
                                                 "end": false,
                                                 "end_value": 0
                          },
                          "load_settings" : {
                                             "load_from_buf": false,
                                             "load_address" : 0,
                                             "load_from_file": false,
                                             "load_file" : ""
                          },
                          "store_settings":{
                                            "store_to_buf": false,
                                            "store_address" : 0 ,
                                            "store_to_file": false,
                                            "store_files" : "",
                                            "file_append" : true
                          },
                          "pins":{
                                 "default": true,
                                 "alt_pins": [],
                                 "pin_high" : [],
                                 "pin_low"  : []
                          }
           
           }
          }      
}

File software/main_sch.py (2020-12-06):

import mono_sch as sch
import json
import board
import busio
import time
import os
from pins import pins
import digitalio
import custom_functions as cf

BUFFERSIZE = 7
BUFFER = bytearray(BUFFERSIZE)
INCREMENT = 1000000 #Offsets timing, 1000000000 = 1 sec per tick, 1000000 = 1 millisecond, 1000 = microsecond, 1 = nanosecond

def add_default_dict(data,default):
    for key in default:
        if type(default[key]) == dict:
            if key not in data:
                data[key] = default[key].copy()
            else:
                data[key] = add_default_dict(data[key], default[key])
        else:
            if key not in data:
                data[key] = default[key]
    return data

def calculate_duration(task, devices):
    if task["duration"] != None:
        return task
    else:
        send_data_size = len(task["connection"]["data"])
        receive_data_size = task["connection"]["data_size"]
        duration = 0
        baud = devices[task["connection"]["device"]]["baud"]

        #IF I2C, addtional duration
        #IF UART additional duration
        #IF SPI additional duration

        if task["load_settings"]["load_from_file"]:
            send_data_size = task["load_settings"]["file_data_size"]
            duration += send_data_size * FILE_READ

        if task["load_settings"]["load_from_buffer"]:
            send_data_size = (task["load_settings"]["load_address_end"]-task["load_settings"]["load_address_start"])
            duration +=  send_data_size* BUFFER_READ

        if task["connection"]["receive"]:
            duration += baud * receive_data_size

        if task["connection"]["send"]:
            duration += baud * send_data_size

        if task["connection"]["pass_through"]:
            baud = devices[task["connection"]["pass_location"]]["baud"]
            duration += baud * receive_data_size

        if task["store_settings"]["store_to_file"]:
            if task["store_settings"]["append"]:
                duration += receive_data_size * FILE_APPEND
            else:
                duration += receive_data_size * FILE_WRITE

        if task["store_settings"]["store_to_buf"]:
            duration += receive_data_size* BUFFER_WRITE

def Com_SPI(data = None, data_size=None, CLK = board.SCK, MOSI=None, MISO= None, slave = None, write_value = 0,  baud=100000, polarity=0, phase=0, bits=8,
            front_data_padding = 0, back_data_padding = 0, start= False, start_value = 0, end = False, end_value = 0, delimiter=""):

    spi = busio.SPI(CLK, MISO=MISO, MOSI=MOSI)
    received = None

    while not spi.try_lock():
        pass

    p = None
    if slave != None:
        p = digitalio.DigitalInOut(pins[slave])
        p.direction = digitalio.Direction.OUTPUT
        p.value = True

    if start:
        spi.write(bytes([int(str(start_value),2)]))

    if data_size != None and data:
        send = bytearray(front_data_padding) + bytearray(data) + bytearray(back_data_padding)
        received = bytearray(data_size)
        write_readinto(received, send)
        if delimiter != "":
            received = str(res)[2:-1].split(delimiter)

    elif data_size != None:
        received = bytearray(data_size)
        received = spi.readinto(received, write_value=write_value)
        if delimiter != "":
            received = str(res)[2:-1].split(delimiter)

    elif data:
        send = bytearray(front_data_padding) + bytearray(data) + bytearray(back_data_padding)
        spi.write(send)

    if end:
        spi.write(bytes([int(str(end_value),2)]))

    if slave != None:
        p.deinit()

    spi.unlock()
    if slave != None:
        p.deinit()
    spi.deinit()
    return received

def run_SPI(task, devices, data):
    res = None

    if task["connection"]["receive"] or task["connection"]["send"]:
        res = Com_SPI(
            data_size = task["connection"]["data_size"],
            data = data,
            delimiter = task["connection"]["data_delimiter"],
            start = task["connection_settings"]["start"],
            start_value = task["connection_settings"]["start_value"],
            end = task["connection_settings"]["end"],
            end_value = task["connection_settings"]["end_value"],
            front_data_padding = task["connection_settings"]["front_data_padding"],
            back_data_padding = task["connection_settings"]["back_data_padding"],
            baud = devices[task["connection"]["device_name"]]["SPI"]["baud"],
            bits = devices[task["connection"]["device_name"]]["SPI"]["bits"],
            polarity = devices[task["connection"]["device_name"]]["SPI"]["polarity"],
            phase = devices[task["connection"]["device_name"]]["SPI"]["phase"],
            write_value = devices[task["connection"]["device_name"]]["SPI"]["write_value"],
            CLK = pins[devices[task["connection"]["device_name"]]["SPI"]["CLK"]],
            MOSI = pins[devices[task["connection"]["device_name"]]["SPI"]["MOSI"]],
            MISO = pins[devices[task["connection"]["device_name"]]["SPI"]["MISO"]],
            )

        if res != None:
            if task["connection"]["pass_through"]:
                Com_SPI(
                    data = res,
                    delimiter = task["connection"]["data_delimiter"],
                    start = task["connection_settings"]["start"],
                    start_value = task["connection_settings"]["start_value"],
                    end = task["connection_settings"]["end"],
                    end_value = task["connection_settings"]["end_value"],
                    front_data_padding = task["connection_settings"]["front_data_padding"],
                    back_data_padding = task["connection_settings"]["back_data_padding"],
                    baud = devices[task["connection"]["device_name"]]["SPI"]["baud"],
                    bits = devices[task["connection"]["device_name"]]["SPI"]["bits"],
                    polarity = devices[task["connection"]["device_name"]]["SPI"]["polarity"],
                    phase = devices[task["connection"]["device_name"]]["SPI"]["phase"],
                    write_value = devices[task["connection"]["device_name"]]["SPI"]["write_value"],
                    CLK = pins[devices[task["connection"]["device_name"]]["SPI"]["CLK"]],
                    MOSI = pins[devices[task["connection"]["device_name"]]["SPI"]["MOSI"]],
                    MISO = pins[devices[task["connection"]["device_name"]]["SPI"]["MISO"]],
                    )

    return res
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

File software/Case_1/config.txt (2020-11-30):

{
 "read_sensor":{
                "deadline" : "Soft",                             
                "duration": 1000,
                "period":   3000,
                "connection" :{
                               "device_name":"Payload",
                               "type": "I2C",
                               "send" : false,
                               "data" : "",
                               "receive": true,
                               "data_size" : 2,
                               "pass_through" : true,
                               "pass_location" : "Coms"
                },
                "connection_settings" : {
                                         "front_data_padding" : 1,
                                         "back_data_padding" : 0,
                                         "start": true,
                                         "start_value": 0,
                                         "end": false,
                                         "end_value": 0
                },
                "load_settings" : {
                                   "load_from_buf": true,
                                   "load_address_start" : 0,
                                   "load_address_end" : 1,
                                   "load_from_file": false,
                                   "load_file" : "",
                                   "load_line" : false,
                                   "start_line": 0,
                                   "end_line":0
                },
                "store_settings":{
                                  "store_to_buf": true,
                                  "store_address" : 0 ,
                                  "store_to_file": true,
                                  "store_file" : "test.txt",
                                  "file_append" : true
                 },
           
           }
}

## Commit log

2020-11-09 Initial Board Designs
    [FlatSat_Final.brd, FlatSat_Final.sch, base_board.brd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]
2020-11-09 Initial Code
    Currently working on implementing figuring out monotonic timeline
2020-11-10 Added initial fully scheduling with BUG
    Currently not scheduling up to full period, in part due to interval being added to the clock each turn
    [mono_sch.py]
2020-11-11 Inital runing of scheduled tasks
    Currently just printing the name of task at task interval
2020-11-15 Updated PCB Designs
    [com_board.brd, com_board.sch, pycubed_non_ext.brd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]
2020-11-18 Updated PCB desgins to fix wiring mismatches
    [FlatSat_Final.brd, FlatSat_Final.sch, com_board.brd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]
2020-11-18 Initial Screen Program ready for adding I2C
2020-11-24 Config works with directory as well as file
    [config.txt]
2020-11-25 demo programs for ESP32
2020-11-27 UART demo
2020-11-27 Updated to work with UART
    [config.txt]
2020-11-30 Added custom functions and tidier scheduler
    [config.txt]
2020-11-30 Added SPI
2020-12-01 Updated PyBoard and added demo files used previously
    [config.txt]
2020-12-03 First prototype payload
2020-12-03 Tidied to be I2C
2020-12-06 Demo programs I2C
2020-12-06 Working interupts
    [config.txt]
2021-01-08 Updated to final Mainboard code
    [config.txt]
2021-01-13 Added missing timing files
    [com.py, main_scheduler.py, timing_append.py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]
2021-01-13 Refactored demo boards code
2021-01-13 Fixed errors in footprints
    [pycubed.sch]
2021-02-22 Final Handover
    [FlatSat_Final.brd, FlatSat_Final.sch, base_board.brd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]
